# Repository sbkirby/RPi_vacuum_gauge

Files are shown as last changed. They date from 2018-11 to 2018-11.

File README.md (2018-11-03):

# Digital Vacuum Regulator with RPi
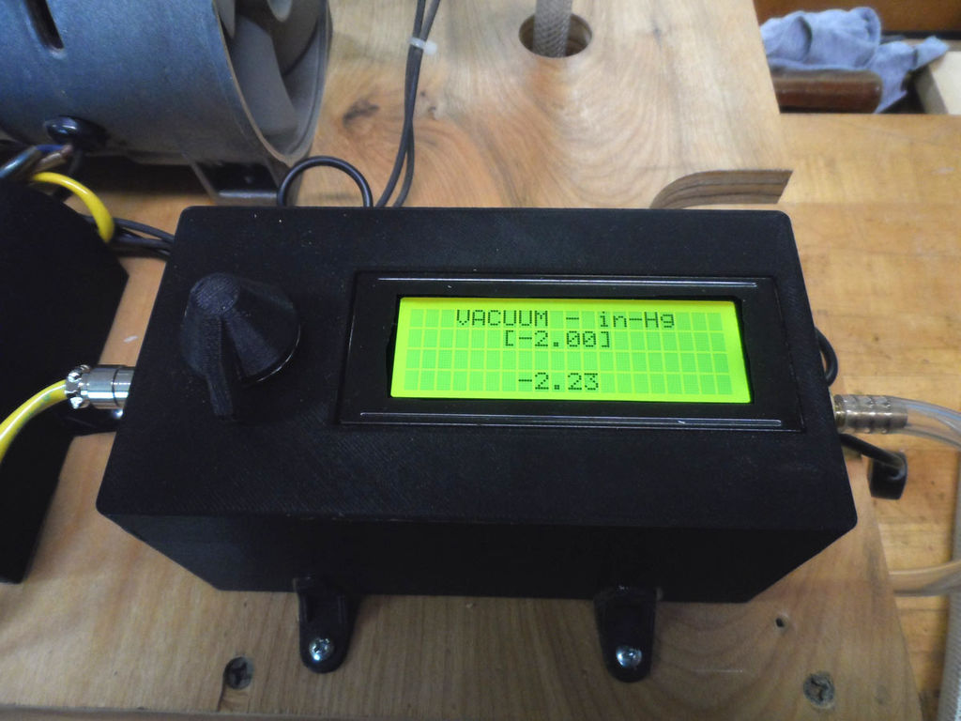
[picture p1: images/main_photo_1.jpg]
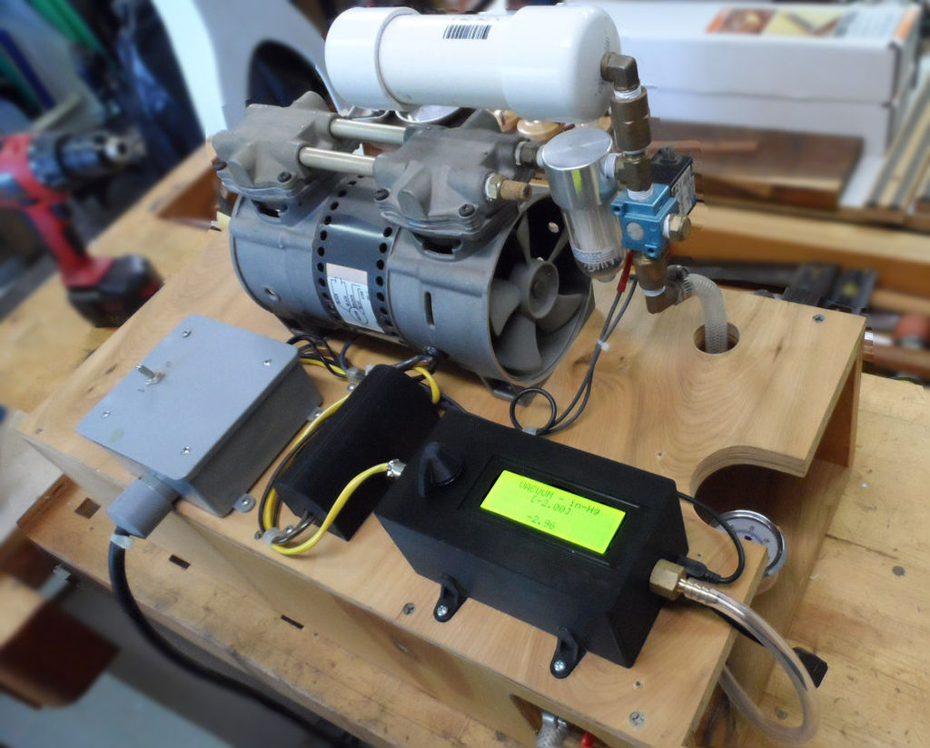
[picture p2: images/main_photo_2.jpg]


This is a Veneer Vacuum Press (Vacuum Pump) which has been modified with a Digital Vacuum Regulator to operate with a selectable vacuum pressure. This device is a replacement for the Vacuum Controller in my DIY Veneer Vacuum Press built with plans from [VeneerSupplies.com](https://www.veneersupplies.com/) or [JoeWoodworking.com](http://www.joewoodworker.com/). These are great plans and the pumps operate very satisfactorily as designed. However, I'm a tinkerer, and I wanted to enhance my pump with the ability to easily and readily control the pressure settings (without a screw driver) over a wider range of pressures with a digitally controlled regulator.

Recently, a need arose which was beyond the lower limits of my Vacuum Controller (Type 1). This project required a Type 2-Vacuum Controller for pressures in the range of 2 to 10 in-Hg. Replacing my Type 1-Vacuum Controller with a Type 2 model was an option, however, this seemed impractical since it would require an additional cost and modifications to switch between the two vacuum ranges. The ideal solution is a single controller with a wider range of pressures (2 to 28 in-Hg).

**Vacuum Controller:** A vacuum controlled micro-switch used to activate a vacuum pump or relay at a selected pressure. The vacuum controller has an adjustment screw that allows you to dial in your desired level of vacuum. The contacts are rated at 10 amps at 120v AC.

### Types of Vacuum Controller
* Type 1 = adjustable for 10.5" to 28" of Hg (Differential 2 to 5" of Hg)
* Type 2 = adjustable for 2" to 10" of Hg (Differential 2 to 4" of Hg)

## Design Considerations
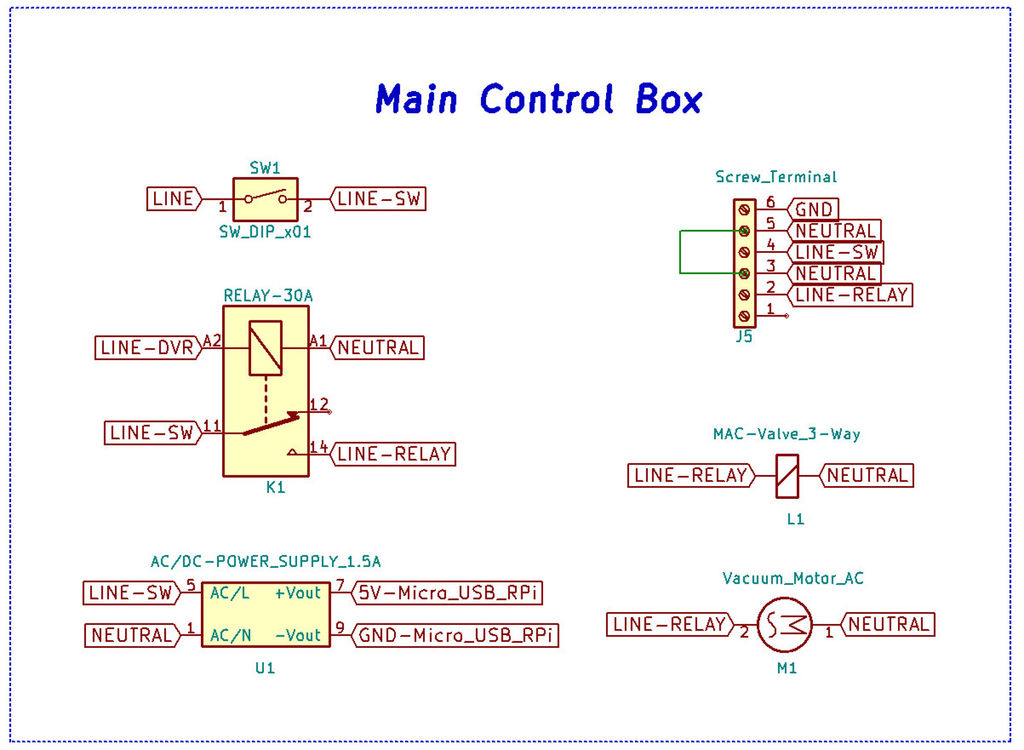
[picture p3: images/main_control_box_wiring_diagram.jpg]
Main Control Box Wiring Diagram


My design replaces the Vacuum Controller with a Digital Vacuum Regulator (DVR). The DVR will be used to control the LINE-DVR line of the RELAY-30A as seen in the Main Control Box schematic. This design requires the addition of a AC/DC 5-VDC Power Supply to Main Control Box for powering the DVR.

This design is capable of maintaining a wide range of vacuum pressures, but the performance is entirely dependent upon the capability of the pump. At the lower pressure range a large CFM pump will maintain these pressures, but result in larger differential pressure swings as a result of the displacement of the pump. This is the case for my 3 CFM pump. It is capable of maintaining 3 in-Hg, but the differential pressure swing is ±1 in-Hg, and the ON cycles of the pump, although infrequent, last approximately one or two seconds. A differential pressure swing of ±1 in-Hg will result with pressures between 141 lbs/ft² to 283 lbs/ft². I have no experience vacuum pressing at these low pressures, therefore I am not sure of the significance of this differential pressure swing. In my opinion, a smaller CFM vacuum pump would probably be more appropriate to maintain these lower vacuum pressures and reduce the differential pressure swings.

The construction of this regulator includes a Raspberry Pi Zero, MD-PS002 Pressure Sensor, HX711 Wheatstone Bridge Amplifier Module, LCD Display, 5V Power Supply, Rotary Encoder and a Relay Module. All of these parts are available from your favorite internet electronics parts suppliers.

I choose a Raspberry Pi (RPi) because python is my preferred programming language, and the support for RPi's is readily available. I am confident this application could be ported to an ESP8266 or other controllers capable of running python. The one disadvantage of the RPi is a Shutdown is highly recommended before powering it down to prevent corruption of the SD Card.

## Parts List

This device is constructed with off the shelf parts including a Raspberry Pi, Pressure Sensor, HX711 Bridge Amplifier, LCD and other parts costing approximately $25.

**PARTS:** 
* 1ea Raspberry Pi Zero - Version 1.3 $5 
* 1ea MD-PS002 Vacuum Sensor Absolute Pressure Sensor $1.75 
* 1ea HX711 Load Cell and Pressure sensor 24 bit AD module $0.75 
* 1ea KY-040 Rotary Encoder Module $1 
* 1ea 5V 1.5A 7.5W Switch Power Module 220V AC-DC Step Down Module $2.56 
* 1ea 2004 20x4 Character LCD Display Module $4.02 
* 1ea 5V 1-Channel Optocoupler Relay Module $0.99 
* 1ea Adafruit Perma-Proto Half-sized Breadboard PCB $4.50 
* 1ea 2N2222A NPN Transistor $0.09 
* 2ea 10K Resistors 
* 1ea Hose Barb Adapter 1/4" ID x 1/4" FIP $3.11 
* 1ea Brass Pipe Square Head Plug 1/4" MIP $2.96 
* 1ea GX12-2 2 Pin Diameter 12mm Male & Female Wire 
* Panel Connector Circular Screw Type Electrical Connector Socket Plug $0.67 
* 1ea Proto Box (or 3D Printed)

## Vacuum Sensor Assembly
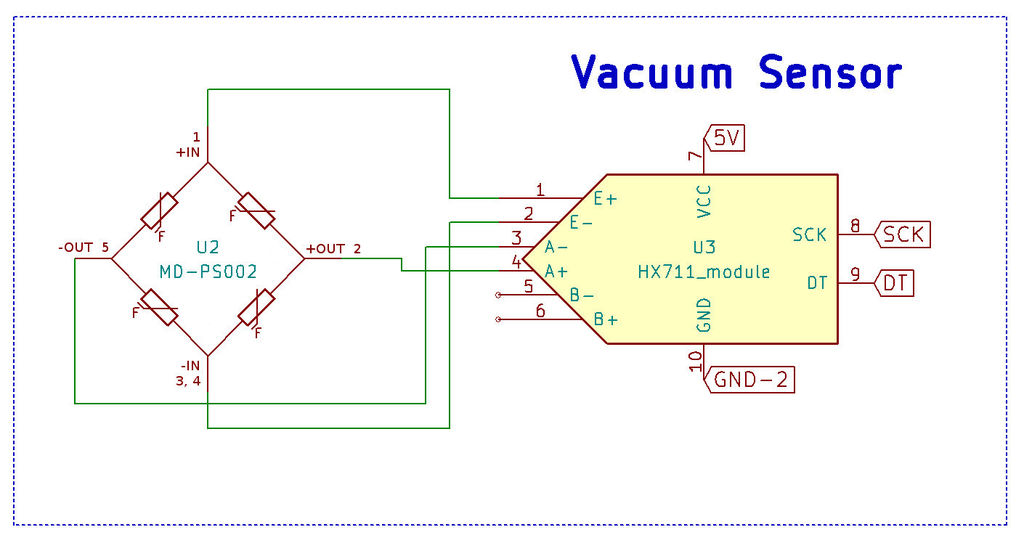
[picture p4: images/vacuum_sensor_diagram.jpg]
Vacuum Sensor Diagram


The MD-PS002 pressure sensor manufactured by Mingdong Technology (Shanghai) Co., Ltd. (MIND) has a range of 150 KPa (absolute pressure). The gauge pressure range (at sea level) for this sensor would be 49 to -101 KPa or 14.5 to -29.6 in-Hg. These sensors are readily available on eBay, banggood, aliexpress and other online sites. However, the specifications listed by a few of these suppliers are conflicting, therefore, I've included a translated "Technical Parameters" sheet from a Mingdong Technology.

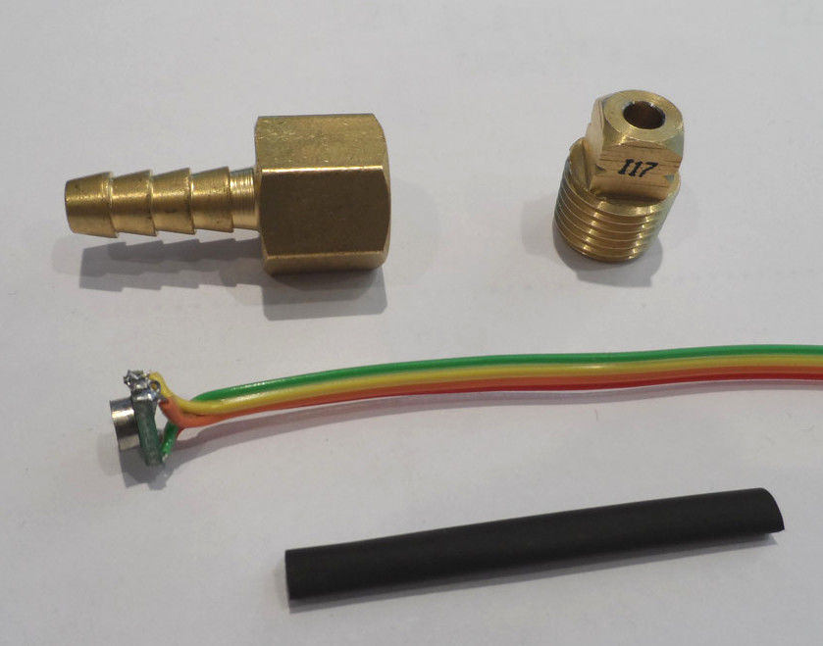
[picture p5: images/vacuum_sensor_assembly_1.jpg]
Vacuum Sensor Assembly


Connecting the sensor to a HX711 Load Cell and Pressure sensor 24 bit AD module requires the following: connect Pins 3 & 4 together; Pin 1 (+IN) to E+; Pin 3 & 4 (-IN) to E-; Pin 2 (+OUT) to A+ and Pin 5 (-OUT) to A- of the HX711 module. Prior to packaging the wired sensor in a brass adapter, cover the leads and the exposed edges of the sensor with heat shrink tubing or electrical tape. Insert and center the sensor over the barbed nipple opening, and then use clear silicone caulking to seal the sensor inside the adapter while taking care to keep the caulking away from the sensor face. A Brass Pipe Square Head Plug which has been drilled with a hole large enough to accommodate the sensor wire is threaded over the wire, filled with silicone caulking and screwed onto the barbed adapter. Wipe excess caulking from the assembly, and wait 24 hours for the caulking to dry before testing.

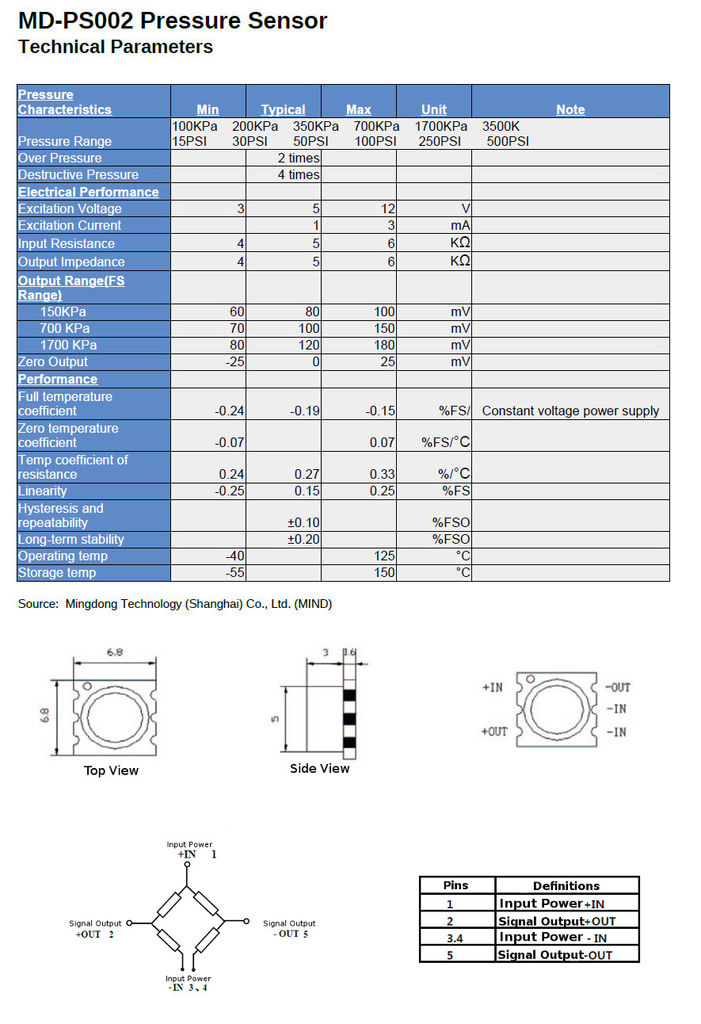
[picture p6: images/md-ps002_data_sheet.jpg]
MD-PS002 Data Sheet


## Electronics Assembly
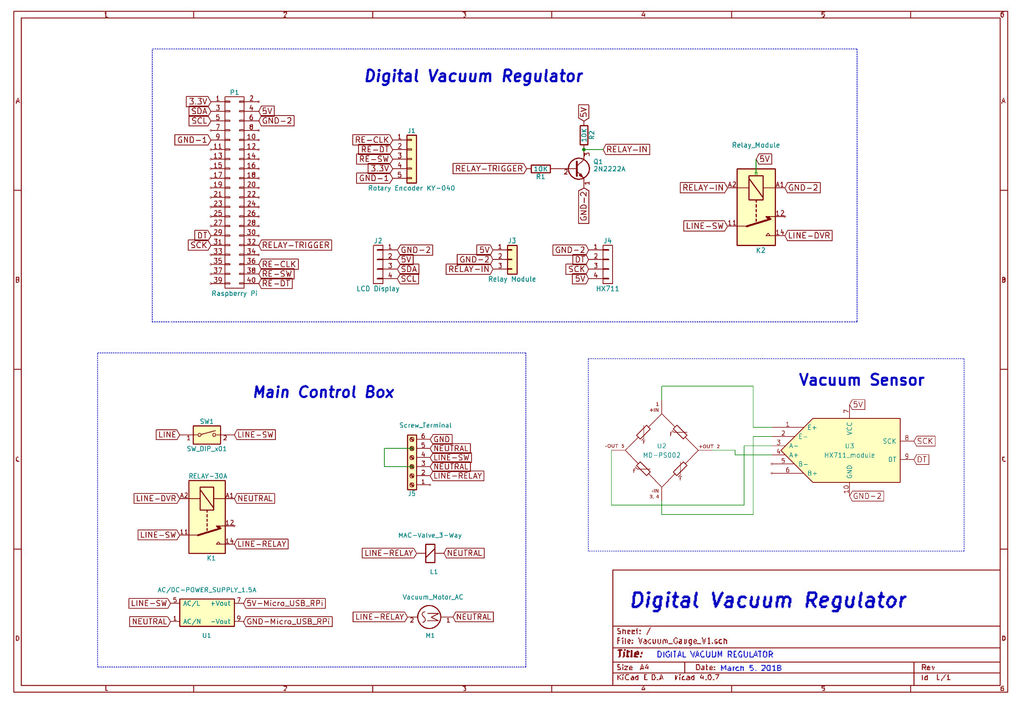
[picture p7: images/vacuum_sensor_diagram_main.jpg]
Main Wiring Diagram


The electronics consist of a Raspberry Pi Zero (RPi) connected to an HX711 module with a MD-PS002 pressure sensor, KY-040 Rotary Encoder, Relay Module and a LCD display. The Rotary Encoder is interfaced to the RPi via Pin 21 to the DT of the encoder, Pin 16 to the CLK and Pin 20 to the SW or switch of the encoder. The pressure sensor is connected to the HX711 module, and the DT and SCK pins of this module are connected directly to Pin 5 and 6 of the RPi. The Relay Module is triggered by a 2N2222A transistor circuit which is connected to RPi Pin 32 for a trigger source. The Normally Open contacts of the Relay Module are connected to LINE-SW and one side of the coil of the 30A RELAY. Power and Ground for the Digital Vacuum Regulator are supplied by Pins 1, 4, 6 and 9 of the RPi. Pin 4 is the 5v power pin, which is connected directly to the RPi's power input. Details of the connections can be seen in the Digital Vacuum Regulator schematic.

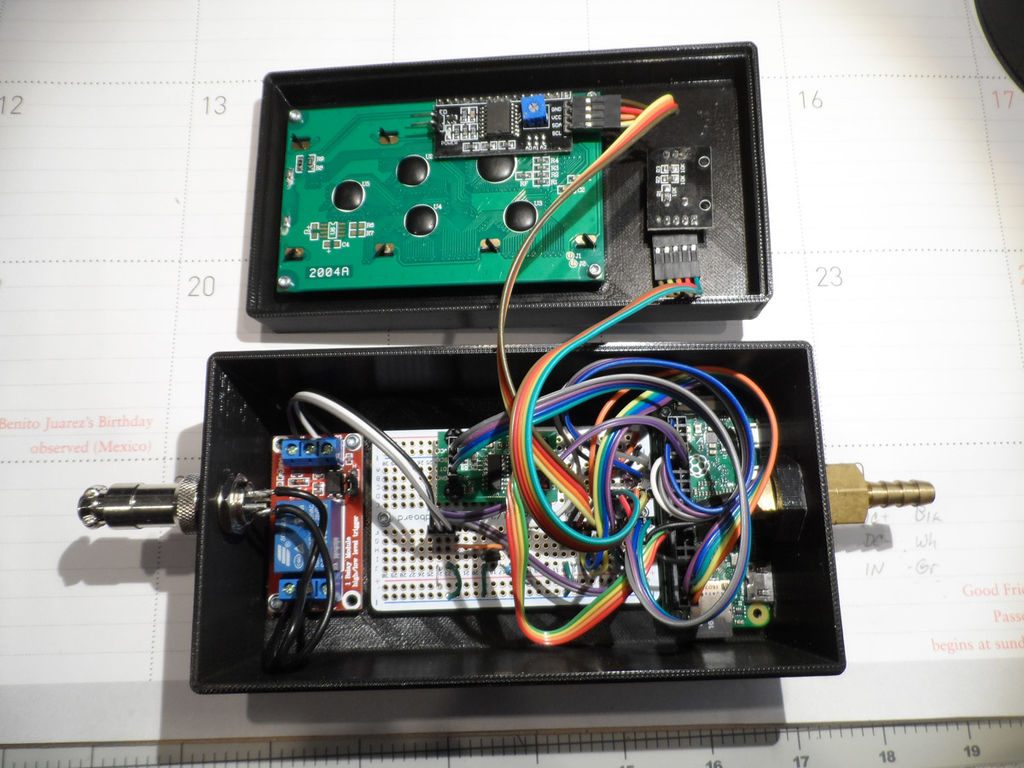
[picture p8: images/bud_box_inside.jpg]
Bud Box Inside


## Update and Configure the Raspberry Pi
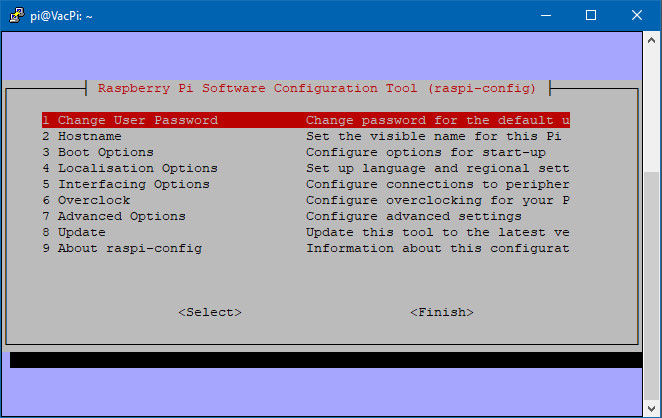
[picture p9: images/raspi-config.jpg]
raspi-config


Update the existing software on your Raspberry Pi (RPi) with the following command lines instructions
```
sudo apt-get update
sudo apt-get upgrade
```
Depending on how out-of-date your RPi is at the time will determine the amount of time needed to complete these commands.
Next, the RPi needs to be configured for I2C communications via Raspi-Config.
```
sudo raspi-config
```
The screen seen above will appear. First select Advanced Options and then Expand Filesystem and select Yes. After returning to the Main Menu of Raspi-Config select Enable Boot to Desktop/Scratch and choose to Boot to Console. From the Main Menu select Advanced Options, and enable I2C and SSH from the available options. Finally, select Finish and reboot the RPi.

## Software
Log into the RPi and create the following directories. The /Vac_Sensor contains the program files and /logs will contain the crontab log files.
```
cd ~
mkdir Vac_Sensor
mkdir logs
cd Vac_Sensor
```
Copy the files above to the /Vac_Sensor folder. I use WinSCP to connect and manage the files on the RPi. Connection to the RPi maybe done via Wifi or serial connection, but SSH needs be enabled in raspi-config to allow this type of connection.

The primary program is vac_sensor.py and may be run from the command prompt. In order to test the script enter the following:
```
sudo python vac_sensor.py
```
As mentioned previously, the vac_sensor.py script is the primary file for the scale. It imports the hx711.py file to read the vacuum sensor via HX711 module. The version of hx711.py used for my project comes from [tatobari/hx711py](https://github.com/tatobari/hx711py). I found this version provided the features I wanted.

The LCD requires the RPi_I2C_driver.py by Denis Pleic and forked by Marty Tremblay, and can be found at [MartyTremblay/RPi_I2C_driver.py](https://gist.github.com/MartyTremblay/7a7fbf76c0c93734511b).

Rotary Encoder by Peter Flocker can be found at [https://github.com/petervflocke/rotaryencoder_rpi](https://github.com/petervflocke/rotaryencoder_rpi)

pimenu by Alan Aufderheide can be found at [https://github.com/skuater/pimenu](https://github.com/skuater/pimenu)

The config.json file contains the data stored by the program, and some items can be modified by menu options. This file is updated and saved at Shutdown. The "units" can be setup via the Units menu option either as in-Hg (default), mm-Hg or psi. The "vacuum_set" is the cutoff pressure, and is stored as in-Hg value, and is modified by the Cutoff Pressure menu option. A "calibration_factor" value is manually set in the config.json file, and is determined by calibrating the vacuum sensor to a vacuum gauge. The "offset" is value created by Tare, and can be set via this menu option. The "cutoff_range" is manually set in the config.json file, and is the differential pressure range of the "vacuum_set" value.

Cutoff Value = "vacuum_set" ± (("cutoff_range"/100) x "vacuum_set")

Please note your "calibration_factor" and "offset" may differ from those I have. Example config.json file:
```
{"units": 0, "vacuum_set": -15.0, "calibration_factor": 230000, "cutoff_range": 0.5, "offset": 11448294}
```

## Calibration
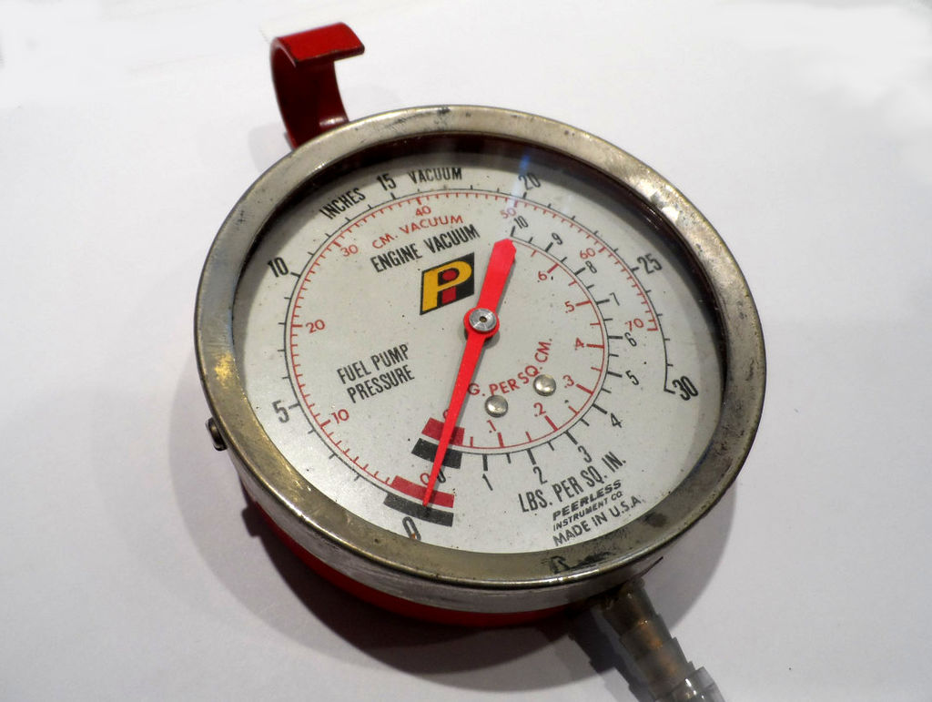
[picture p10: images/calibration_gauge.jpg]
Calibration Gauge


Calibration is much easier to do using SSH and running the following commands:
```
cd Vac_Sensor 
sudo python vac_sensor.py
```
Exiting the python script can be done via Ctrl-C, and modifications can be made to the /Vac_Sensor/config.json file.

Calibrating the vacuum sensor requires an accurate vacuum gauge, and adjusting the "calibration_factor" to match the output displayed on the LCD. First, use the Tare menu option to set and save the "offset" value with the pump at atmospheric pressure. Next, turn the pump ON with the Vacuum menu and after the pressure settles read the LCD display and compare this to vacuum gauge. Turn the pump OFF and Exit the script. Adjust the "calibration_factor" variable located in /Vac_Sensor/config.json file. Restart the script and repeat the process with exception of Tare. Make the necessary adjustments to the "calibration_factor" until the LCD display matches the gauge reading.

The "calibration_factor" and "offset" affect the display via the following calculations:

get_value = read_average - "offset"

pressure = get_value/"calibration_factor"

I used an old Peerless Engine Vacuum Gauge to calibrate the regulator instead of the vacuum gauge on my pump because it had been knocked out calibration. The Peerless gauge is 3-3/4" (9.5 cm) in diameter and much easier to read.

## Run at Startup
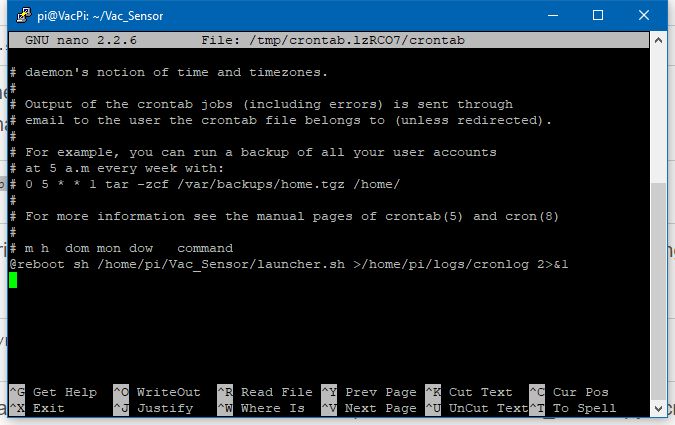
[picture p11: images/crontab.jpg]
Crontab


There's an excellent Instructable [Raspberry Pi: Launch Python script on startup](https://www.instructables.com/id/Raspberry-Pi-Launch-Python-script-on-startup/?ALLSTEPS) for running a scripts at startup.

Log into the RPi and change to the /Vac_Sensor directory.
```
cd /Vac_Sensor
nano launcher.sh
```
Include the following text in launcher.sh
```
#!/bin/sh
# launcher.sh
# navigate to home directory, then to this directory, then execute python script, then back home
cd /
cd home/pi/Vac_Sensor
sudo python vac_sensor.py
cd /
```
Exit and save the launcher.sh

We need to make the script an executable.
```
chmod 755 launcher.sh
```
Test the script.
```
sh launcher.sh
```
Next, we need to edit crontab (the linux task manager) to launch the script at startup. Note: we have already created the /logs directory previously.
```
sudo crontab -e
```
This will bring the crontab window as seen above. Navigate to the end of the file and enter the following line.
```
@reboot sh /home/pi/Vac_Sensor/launcher.sh >/home/pi/logs/cronlog 2>&1
```
Exit and save the file, and reboot the RPi. The script should start the vac_sensor.py script after the RPi reboots. The status of the script can be checked in the log files located in the /logs folder.

## Operational Instructions

For Operational Instructions visit [Digital Vacuum Regulator](https://www.instructables.com/id/Digital-Vacuum-Regulator/) on Instructables.

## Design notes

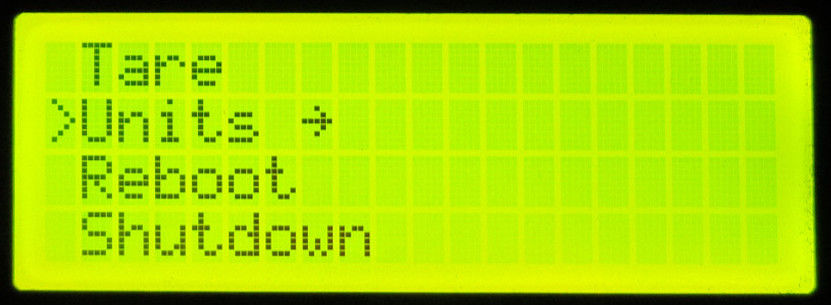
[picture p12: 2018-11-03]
images/menu_units.jpg

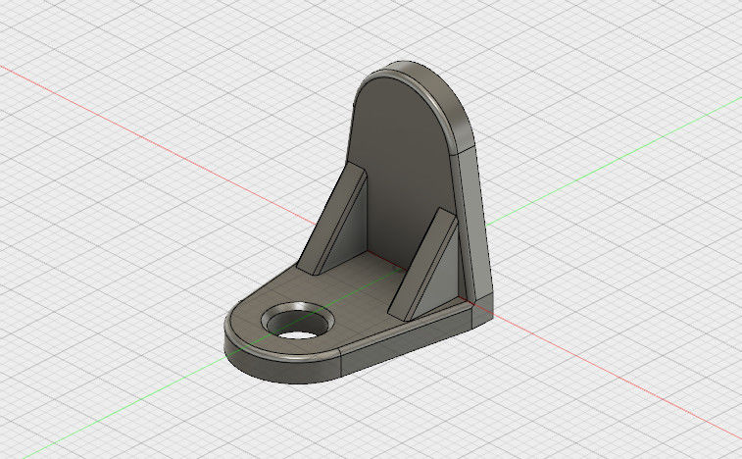
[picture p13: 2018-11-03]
images/model_of_tab.jpg

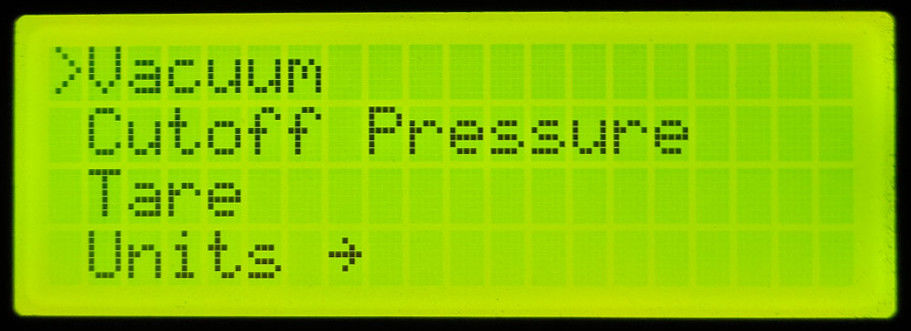
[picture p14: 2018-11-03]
images/main_menu.jpg

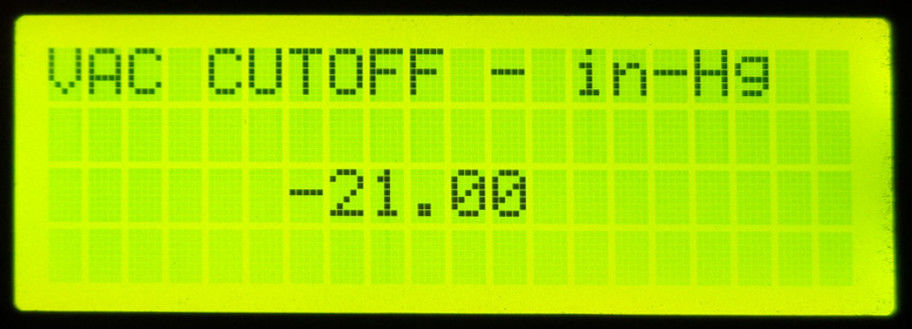
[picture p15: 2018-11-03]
images/cutoff_pressure.jpg

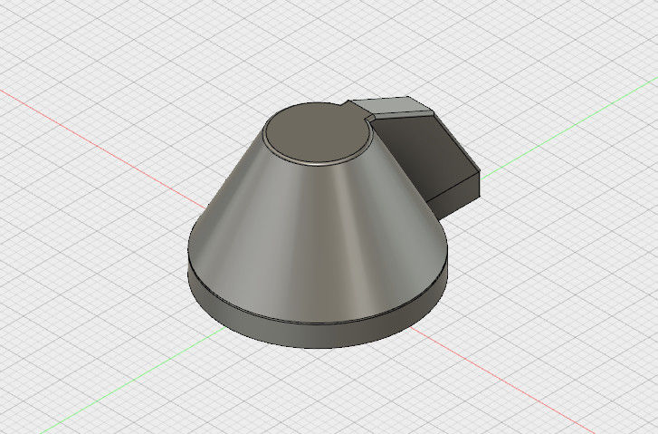
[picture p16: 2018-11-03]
images/model_of_knob.jpg

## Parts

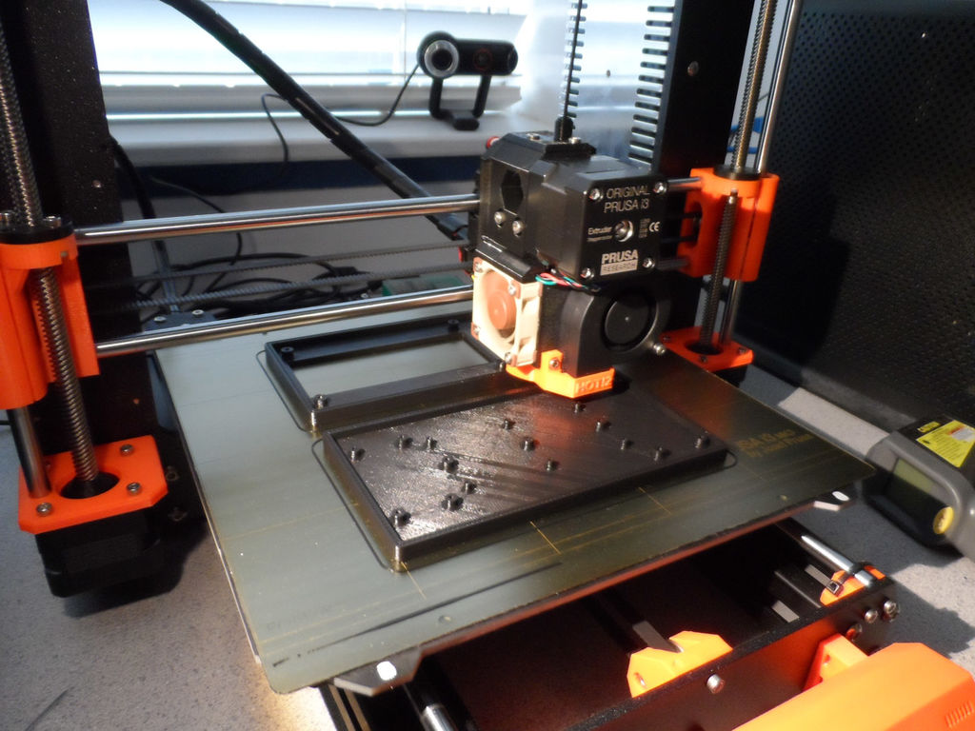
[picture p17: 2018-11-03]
images/3d_printing_parts.jpg

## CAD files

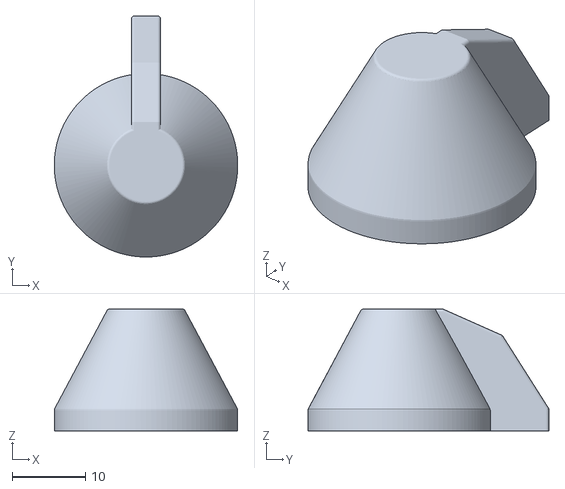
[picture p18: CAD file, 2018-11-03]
stl/Knob_for_KY-040_Rotary_Encoder.stl
25.0 x 32.8 x 16.6

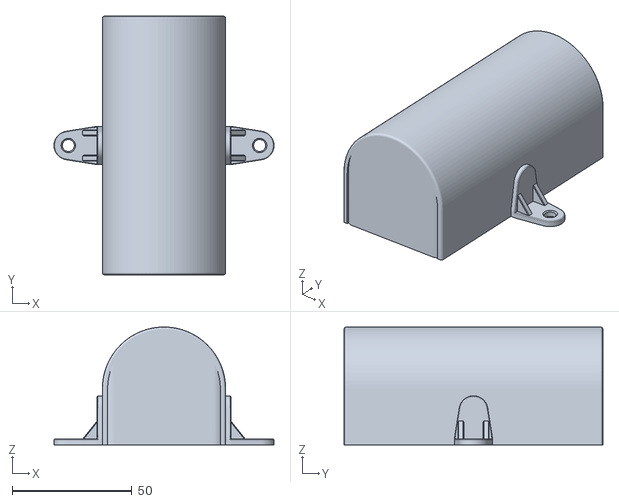
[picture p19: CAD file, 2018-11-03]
stl/Capacitor_Cover.stl
91.8 x 108.0 x 49.2

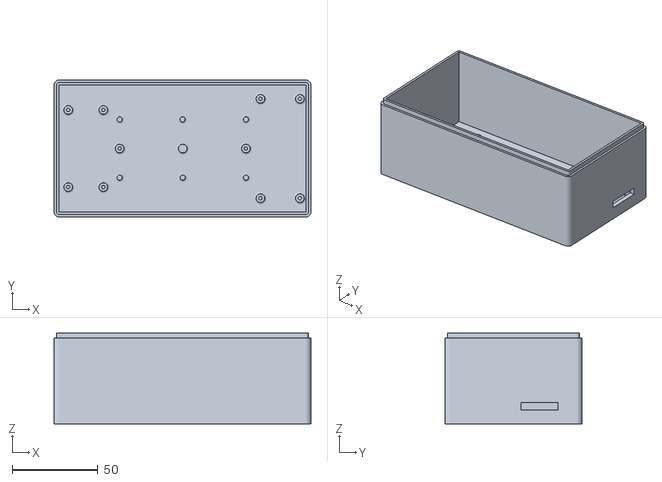
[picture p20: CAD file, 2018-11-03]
stl/Base.stl
150.0 x 80.0 x 53.0

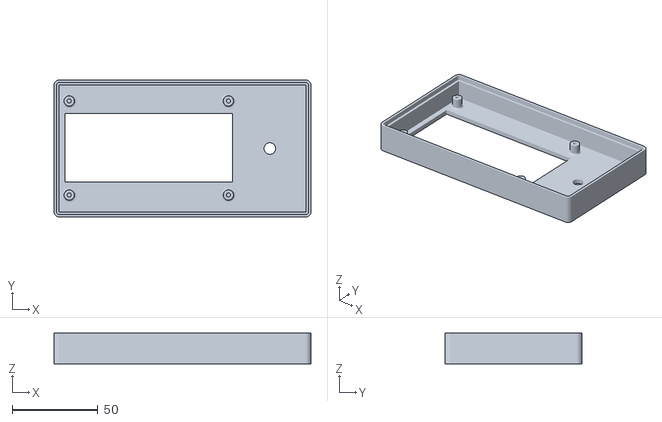
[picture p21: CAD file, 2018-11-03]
stl/Top.stl
150.0 x 80.0 x 18.0

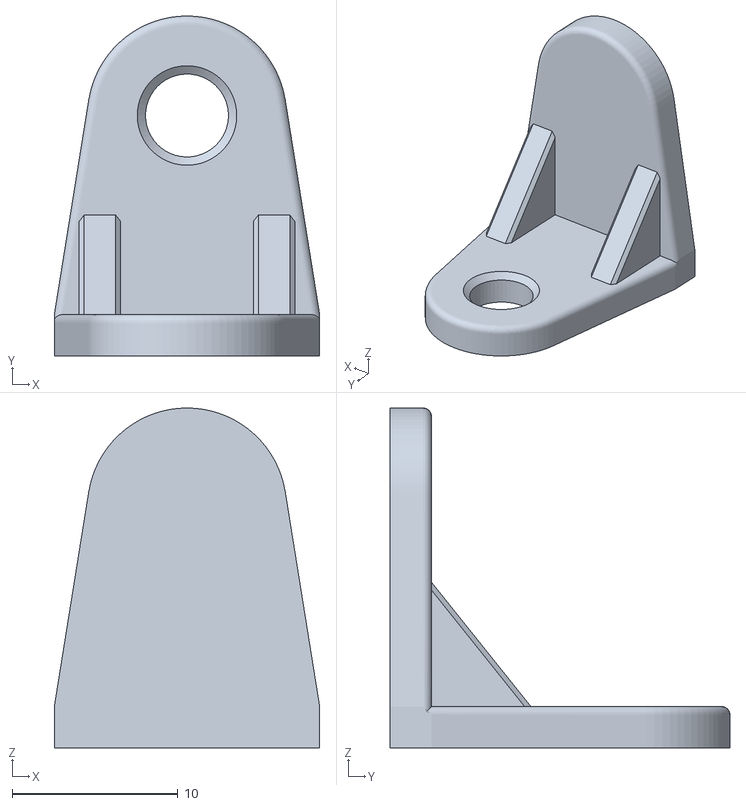
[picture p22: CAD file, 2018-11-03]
stl/Screw_Bracket.stl
16.0 x 20.5 x 20.5

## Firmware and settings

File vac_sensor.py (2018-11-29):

#!/usr/bin/python
#
# Originally lcdmenu.py created by Alan Aufderheide, February 2013
# Modified by Stephen Kirby, November 2017
#
# This provides a menu driven application using the Adafruit_CharLCDPlate
# driver

import commands
import os
from string import split
from time import sleep, strftime, localtime
from datetime import datetime, timedelta
from xml.dom.minidom import *

import smbus

import json
import sys
from Queue import Queue
import RotaryEncoder
import RPi_I2C_driver
from hx711 import HX711
import RPi.GPIO as GPIO

# Load configuration from config JSON file.
with open('config.json', 'r') as infile:
    config = json.load(infile)

menu_file = 'vac_menu.xml' # Menu Tree

# Rotary Encoder wiring
A_PIN  = 21 # A pin on rotary encoder or DT on KY040
B_PIN  = 16 # B pin on rotary encoder or CLK on KY040
SW_PIN = 20 # press pin on rotary or SW on KY040

# Init Queue and Encoder
RotQueue = Queue()                                                              # define global queue for events
encoder = RotaryEncoder.RotaryEncoderWorker(A_PIN, B_PIN, SW_PIN, RotQueue)     # create a new rotary switch

# set DEBUG=1 for print debug statements
DEBUG = 0
DISPLAY_ROWS = 4
DISPLAY_COLS = 20

# set to 0 if you want the LCD to stay on, 1 to turn off and on auto
AUTO_OFF_LCD = 0

# Menu Folders to display Selected items
menu_select = ["units"]

# init LCD
lcd = RPi_I2C_driver.lcd()
lcd.lcd_clear()
lcd.backlight(1) # turn ON LED

# HX711(dout, sck) - initialize Wheatstone Bridge amplifier
hx = HX711(5, 6)  # DOUT = GPIO.IN, SCK = GPIO.OUT
# The value on the Gauge = value / self.REFERENCE_UNIT
hx.set_reference_unit(config['calibration_factor'])
# Reset and set offset for the HX711 amplifier board
hx.reset()
hx.set_offset(config['offset']) # set offset for MD-PS002 Pressure Sensor
hx.tare(5) # with no Vacuum on Sensor

# Init GPIO output port for Relay control
GPIO.setmode(GPIO.BCM)
GPIO.setup(12, GPIO.OUT)
GPIO.output(12, False) # Turn OFF Relay

# save data to config.json data file
def save_data():
    with open('config.json', 'w') as outfile:
        json.dump(config, outfile)

# save the data, cleanup GPIO and exit
def clean_and_exit(doExit):
    save_data() # save data file
    lcd.lcd_clear() # clear LCD
    sleep(0.1)
    lcd.backlight(0) # turn OFF LED
    sleep(0.1)
    GPIO.cleanup() # cleanup GPIO
    if doExit:
        sys.exit() #exit python to system

def DoShutdown():
    lcd.lcd_clear()
    lcd.message("Shutting Down!")
    sleep(3)
    clean_and_exit(False)
    commands.getoutput("sudo shutdown -h now")

def DoReboot():
    lcd.lcd_clear()
    lcd.message("I'm Rebooting!")
    sleep(3)
    clean_and_exit(False)
    commands.getoutput("sudo reboot")

# Go BACK in the Menu
def DoBack():
    lcd.lcd_clear()
    display.update('l')
    #display.update('s')
    display.display()
    sleep(0.05)

# Calculate Cutoff range
def SetCutoffRange(state):
    # Range of Vacuum Pump activation
    cutoff_range = config['cutoff_range'] / 100
    if state == 'ON':
        return (-cutoff_range * config["vacuum_set"]) + config["vacuum_set"]
    if state == 'OFF':
        return (cutoff_range * config["vacuum_set"]) + config["vacuum_set"]

# Fetch Units String
def GetUnit():
    if config['units'] == 0: # in-Hg    DEFAULT
        unit = 'in-Hg'
    elif config['units'] == 1: # mm-Hg
        unit = 'mm-Hg'
    elif config['units'] == 2: # psi
        unit = 'psi'
    return unit

# Convert from in-Hg to other units
def ConvertVac(vac):
    if config['units'] == 0: # in-Hg    DEFAULT
        vac *= 1.0
    elif config['units'] == 1: # mm-Hg
        vac *= 25.3285
    elif config['units'] == 2: # psi
        vac *= 0.48977
    return vac

# Select Units
def SetinHg(): #DEFAULT
    config['units'] = 0
    display.display()

def SetmmHg():
    config['units'] = 1
    display.display()

def Setpsi():
    config['units'] = 2
    display.display()

# Display Vacuum and Cutoff on LCD Display
def DoDisplay():
    lcd.lcd_clear()
    unit = GetUnit()
    VacSet = ConvertVac(config['vacuum_set'])
    VacSetOFF = ConvertVac(SetCutoffRange('OFF'))
    VacSetON = ConvertVac(SetCutoffRange('ON'))
    GPIO.output(12, False) # Turn OFF Relay
    if DEBUG:
        print('OFF: {0:.2f}'.format(VacSetOFF) + ' ' + unit)
        print('ON: {0:.2f}'.format(VacSetON) + ' ' + unit)

    while True:
        # Read Vacuum Sensor
        val = VacVal = ConvertVac(hx.get_weight(1))
        if DEBUG:
            print('{0:.2f}'.format(VacVal) + ' ' + unit)
        # Monitor Vacuum Cutoff Value
        if VacVal <= VacSetOFF:
            GPIO.output(12, False) # Turn OFF Relay
            #sleep(0.05)
        elif VacVal > VacSetON:
            GPIO.output(12, True) # Turn ON Relay
            #sleep(0.05)
        # Display Results
        lcd.home()
        lcd.message('   VACUUM - ' + unit + '\n      [{0:.2f}]'.format(VacSet) + '\n\n')
        lcd.message('       {0:.2f}'.format(val))
        # Reset Wheatstone Bridge
        hx.power_down()
        hx.power_up()
        # Read RotaryEncoder
        if not(RotQueue.empty()):
            m = RotQueue.get_nowait()
            if (m == RotaryEncoder.EventDown): #SELECT
                GPIO.output(12, False) # Turn OFF Relay on Exit
                RotQueue.task_done()
                DoBack()
                return
            RotQueue.task_done()

# Display and set Cutoff Vacuum
def SetCutoff():
    lcd.lcd_clear()
    unit = GetUnit()
    while True:
        # Prints the weight. Comment if you're debbuging the MSB and LSB issue.
        val = ConvertVac(config["vacuum_set"]) # Stored in in-Hg reguardless of units selected
        if DEBUG:
            print('{0:.2f}'.format(val) + ' ' + unit)
        lcd.home()
        lcd.message('VAC CUTOFF - ' + unit + '\n\n')
        lcd.message('      {0:.2f}'.format(val))
        # Read RotaryEncoder
        if not(RotQueue.empty()):
            m = RotQueue.get_nowait()
            if (m == RotaryEncoder.EventDown): #SELECT - Exit
                RotQueue.task_done()
                DoBack()
                return
            if (m == RotaryEncoder.EventLeft): #LEFT - Subtract
                config["vacuum_set"] -= 0.25
            if (m == RotaryEncoder.EventRight): #RIGHT - Add
                config["vacuum_set"] += 0.25
            RotQueue.task_done()

# Tare Vacuum Sensor
def DoTare():
    lcd.lcd_clear()
    lcd.message('\n Tare Vac Sensor\n')
    hx.reset()
    hx.set_offset(config['offset']) # set offset for MD-PS002 Pressure Sensor
    hx.tare(5) # with no Vacuum on Sensor
    config['offset'] = hx.OFFSET # read and store the OFFSET
    save_data() # save the new OFFSET to config.json data file
    sleep(3)

def ShowIPAddress():
    if DEBUG:
        print('in ShowIPAddress')
    lcd.lcd_clear()
    lcd.message(commands.getoutput("/sbin/ifconfig").split("\n")[1].split()[1][5:])
    while True:
        if not(RotQueue.empty()):
            m = RotQueue.get_nowait()
            if (m == RotaryEncoder.EventDown): #SELECT
                DoBack()
                return
            RotQueue.task_done()

# Classes Used in Menus
class CommandToRun:
    def __init__(self, myName, theCommand):
        self.text = myName
        self.commandToRun = theCommand
    def Run(self):
        self.clist = split(commands.getoutput(self.commandToRun), '\n')
        if len(self.clist) > 0:
            lcd.lcd_clear()
            lcd.message(self.clist[0])
            lcd.crlf()
            for i in range(1, len(self.clist)):
                while not(RotQueue.empty()):
                    m=RotQueue.get_nowait()
                    if m == RotaryEncoder.EventLeft: #DOWN
                        break
                    RotQueue.task_done()
                    #sleep(0.25)
                lcd.lcd_clear()
                lcd.message(self.clist[i-1]+'\n'+self.clist[i])
                lcd.crlf()
                sleep(0.5)
        while not(RotQueue.empty()):
            m=RotQueue.get_nowait()
            if m == RotaryEncoder.EventRight:  #UP
                break
            RotQueue.task_done()

class Widget:
    def __init__(self, myName, myFunction):
        self.text = myName
        self.function = myFunction

class Folder:
    def __init__(self, myName, myParent):
        self.text = myName
        self.items = []
        self.parent = myParent

# Process menu items based on type
def ProcessNode(currentNode, currentItem):
    children = currentNode.childNodes

    for child in children:
        if isinstance(child, xml.dom.minidom.Element):
            if child.tagName == 'folder':
                thisFolder = Folder(child.getAttribute('text'), currentItem)
                currentItem.items.append(thisFolder)
                ProcessNode(child, thisFolder)
            elif child.tagName == 'widget':
                thisWidget = Widget(child.getAttribute('text'), child.getAttribute('function'))
                currentItem.items.append(thisWidget)
            elif child.tagName == 'run':
                thisCommand = CommandToRun(child.getAttribute('text'), child.firstChild.data)
                currentItem.items.append(thisCommand)

class Display:
    def __init__(self, folder):
        self.curFolder = folder
        self.curTopItem = 0
        self.curSelectedItem = 0
    def display(self):
        isSelected = match_selected = ''
        # Check for Bottom of items list
        if self.curTopItem > len(self.curFolder.items) - DISPLAY_ROWS:
            self.curTopItem = len(self.curFolder.items) - DISPLAY_ROWS
        # Check for Top of items list
        if self.curTopItem < 0:
            self.curTopItem = 0
        if DEBUG:
            print('------------------')
        if self.curFolder.text[0:self.curFolder.text.find(' ')].lower() in menu_select:
            isSpace = self.curFolder.text.find(' ')
            if isSpace < 0:
                isSpace = self.curFolder.text.len()
            isSelected = self.curFolder.text[0:isSpace].lower()
        str = ''
        for row in range(self.curTopItem, self.curTopItem + DISPLAY_ROWS):
            if isSelected != '':
                if isSelected == 'units':
                    match_selected = GetUnit()
            if row > self.curTopItem:
                str += '\n'
            if row < len(self.curFolder.items):
                # Is row the current selected line
                if row == self.curSelectedItem:
                    # Current line with cursor
                    cmd = '>' + self.curFolder.items[row].text
                    if self.curFolder.items[row].text.lower() == match_selected.lower():
                        cmd += '*'
                    if len(cmd) < DISPLAY_COLS:
                        # Add spaces to END of line
                        for row in range(len(cmd), DISPLAY_COLS):
                            cmd += ' '
                    if DEBUG:
                        print('|'+cmd+'|')
                    str += cmd
                # If NOT currently selected line
                else:
                    # Lines without cursor - Add space for NO cursor
                    cmd = ' '+self.curFolder.items[row].text
                    if self.curFolder.items[row].text.lower() == match_selected.lower():
                        cmd += '*'
                    if len(cmd) < DISPLAY_COLS:
                        # Add spaces to END of line
                        for row in range(len(cmd), DISPLAY_COLS):
                            cmd += ' '
                    if DEBUG:
                        print('|'+cmd+'|')
                    str += cmd
        if DEBUG:
            print('------------------')
        lcd.lcd_clear()
        lcd.home()
        lcd.message(str)

    # Orignal update() designed for LCD with 4 Buttons (Left, Right, Up, Down)
    # This function has been utilized as follows:
    # UP = Clockwise knob turn
    # DOWN = Counter clockwise knob turn
    # SELECT = Press knob DOWN
    def update(self, command):
        global currentLcd
        global lcdstart
        #lcd.backlight(currentLcd)
        lcdstart = datetime.now()
        if DEBUG:
            print('do',command)
        if command == 'u':
            self.up()
        elif command == 'd':
            self.down()
        elif command == 'r':
            self.right()
        elif command == 'l':
            self.left()
        elif command == 's':
            self.select()

    def up(self):
        if self.curSelectedItem == 0:
            return
        elif self.curSelectedItem > self.curTopItem:
            self.curSelectedItem -= 1
        else:
            self.curTopItem -= 1
            self.curSelectedItem -= 1

    def down(self):
        if self.curSelectedItem+1 == len(self.curFolder.items):
            return
        elif self.curSelectedItem < self.curTopItem+DISPLAY_ROWS-1:
            self.curSelectedItem += 1
        else:
            self.curTopItem += 1
            self.curSelectedItem += 1

    def left(self):
        if isinstance(self.curFolder.parent, Folder):
            # find the current in the parent
            itemno = 0
            index = 0
            for item in self.curFolder.parent.items:
                if self.curFolder == item:
                    if DEBUG:
                        print('foundit')
                    index = itemno
                else:
                    itemno += 1
            if index < len(self.curFolder.parent.items):
                self.curFolder = self.curFolder.parent
                self.curTopItem = index
                self.curSelectedItem = index
            else:
                self.curFolder = self.curFolder.parent
                self.curTopItem = 0
                self.curSelectedItem = 0

    def right(self):
        if isinstance(self.curFolder.items[self.curSelectedItem], Folder):
            self.curFolder = self.curFolder.items[self.curSelectedItem]
            self.curTopItem = 0
            self.curSelectedItem = 0
        elif isinstance(self.curFolder.items[self.curSelectedItem], Widget):
            if DEBUG:
                print('eval', self.curFolder.items[self.curSelectedItem].function)
            eval(self.curFolder.items[self.curSelectedItem].function+'()')
        elif isinstance(self.curFolder.items[self.curSelectedItem], CommandToRun):
            self.curFolder.items[self.curSelectedItem].Run()

    def select(self):
        if DEBUG:
            print('check widget')
        if isinstance(self.curFolder.items[self.curSelectedItem], Widget):
            if DEBUG:
                print('eval', self.curFolder.items[self.curSelectedItem].function)
            eval(self.curFolder.items[self.curSelectedItem].function+'()')

# Process Rotary Encoder Actions with a Queue
def process():
    # this function can be called in order to decide what is happening with the switch
    while True:
        if not(RotQueue.empty()):
            m=RotQueue.get_nowait()
            # DOWN = Counter clockwise knob turn
            if m == RotaryEncoder.EventLeft: #DOWN
                display.update('d') #DOWN
                display.display()
                sleep(0.1)
            # SELECT = Press knob DOWN
            if m == RotaryEncoder.EventDown: #SELECT
                display.update('r') #RIGHT
                #display.update('s') #SELECT
                display.display()
                sleep(0.1)
            # UP = Clockwise knob turn
            if m == RotaryEncoder.EventRight: #UP
                display.update('u') #UP
                display.display()
                sleep(0.1)

            if AUTO_OFF_LCD:
                lcdtmp = lcdstart + timedelta(seconds=5)
                if (datetime.now() > lcdtmp):
                    #lcd.backlight(lcd.OFF)
                    #sleep(0.1)
                    pass
            RotQueue.task_done()

# now start things up
uiItems = Folder('root','')

dom = parse(menu_file) # parse an XML file by name

top = dom.documentElement

currentLcd = False
#lcd.backlight(lcd.OFF)
ProcessNode(top, uiItems)

display = Display(uiItems)
display.display()

if DEBUG:
    print('start while')

lcdstart = datetime.now()

if __name__ == "__main__":
    try:
        while True:
            if DEBUG:
                print('__main__')
            #sleep (0.01)  # here you can process on RPI whatever you want and operate the rotary knob it won't be missed
            process()  # and check what has happened with rotary
    except KeyboardInterrupt:
        print('broken by keyboard')
        clean_and_exit(True)

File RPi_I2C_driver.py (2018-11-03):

# -*- coding: utf-8 -*-
"""
Compiled, mashed and generally mutilated 2014-2015 by Denis Pleic
Made available under GNU GENERAL PUBLIC LICENSE

# Modified Python I2C library for Raspberry Pi
# as found on http://www.recantha.co.uk/blog/?p=4849
# Joined existing 'i2c_lib.py' and 'lcddriver.py' into a single library
# added bits and pieces from various sources
# By DenisFromHR (Denis Pleic)
# 2015-02-10, ver 0.1

A large amount of the code was included from Adafruit_CharLCDPlate

"""
#
#
import smbus
from time import *

class i2c_device:
   def __init__(self, addr, port=1):
      self.addr = addr
      self.bus = smbus.SMBus(port)

# Write a single command
   def write_cmd(self, cmd):
      self.bus.write_byte(self.addr, cmd)
      sleep(0.0001)

# Write a command and argument
   def write_cmd_arg(self, cmd, data):
      self.bus.write_byte_data(self.addr, cmd, data)
      sleep(0.0001)

# Write a block of data
   def write_block_data(self, cmd, data):
      self.bus.write_block_data(self.addr, cmd, data)
      sleep(0.0001)

# Read a single byte
   def read(self):
      return self.bus.read_byte(self.addr)

# Read
   def read_data(self, cmd):
      return self.bus.read_byte_data(self.addr, cmd)

# Read a block of data
   def read_block_data(self, cmd):
      return self.bus.read_block_data(self.addr, cmd)



class lcd:
    # LCD Address
    ADDRESS = 0x27

    # commands
    LCD_CLEARDISPLAY = 0x01
    LCD_RETURNHOME = 0x02
    LCD_ENTRYMODESET = 0x04
    LCD_DISPLAYCONTROL = 0x08
    LCD_CURSORSHIFT = 0x10
    LCD_FUNCTIONSET = 0x20
    LCD_SETCGRAMADDR = 0x40
    LCD_SETDDRAMADDR = 0x80

    # flags for display entry mode
    LCD_ENTRYRIGHT = 0x00
    LCD_ENTRYLEFT = 0x02
    LCD_ENTRYSHIFTINCREMENT = 0x01
    LCD_ENTRYSHIFTDECREMENT = 0x00

    # flags for display on/off control
    LCD_DISPLAYON = 0x04
    LCD_DISPLAYOFF = 0x00
    LCD_CURSORON = 0x02
    LCD_CURSOROFF = 0x00
    LCD_BLINKON = 0x01
    LCD_BLINKOFF = 0x00

    # flags for display/cursor shift
    LCD_DISPLAYMOVE = 0x08
    LCD_CURSORMOVE = 0x00
    LCD_MOVERIGHT = 0x04
    LCD_MOVELEFT = 0x00

    # flags for function set
    LCD_8BITMODE = 0x10
    LCD_4BITMODE = 0x00
    LCD_2LINE = 0x08
    LCD_1LINE = 0x00
    LCD_5x10DOTS = 0x04
    LCD_5x8DOTS = 0x00

    # flags for backlight control
    LCD_BACKLIGHT = 0x08
    LCD_NOBACKLIGHT = 0x00

    # Offset for up to 4 rows.
    LCD_ROW_OFFSETS         = (0x00, 0x40, 0x14, 0x54)

    # Line addresses for up to 4 line displays.  Maps line number to DDRAM address for line.
    LINE_ADDRESSES = { 1: 0xC0, 2: 0x94, 3: 0xD4 }

    # Truncation constants for message function truncate parameter.
    NO_TRUNCATE       = 0
    TRUNCATE          = 1
    TRUNCATE_ELLIPSIS = 2

    En = 0b00000100 # Enable bit
    Rw = 0b00000010 # Read/Write bit
    Rs = 0b00000001 # Register select bit

    #initializes objects and lcd
    def __init__(self):
        self.lcd_device = i2c_device(self.ADDRESS)

        # Initialize display control, function, and mode registers.
        self.displaycontrol = self.LCD_DISPLAYON | self.LCD_CURSOROFF | self.LCD_BLINKOFF
        self.displayfunction = self.LCD_4BITMODE | self.LCD_1LINE | self.LCD_2LINE | self.LCD_5x8DOTS
        self.displaymode = self.LCD_ENTRYLEFT | self.LCD_ENTRYSHIFTDECREMENT

        self.lcd_write(0x03)
        self.lcd_write(0x03)
        self.lcd_write(0x03)
        self.lcd_write(0x02)

        # Write registers.
        self.lcd_write(self.LCD_DISPLAYCONTROL | self.displaycontrol)
        self.lcd_write(self.LCD_FUNCTIONSET | self.displayfunction)
        self.lcd_write(self.LCD_ENTRYMODESET | self.displaymode)  # set the entry mode

        sleep(0.2)

    # clocks EN to latch command
    def lcd_strobe(self, data):
        self.lcd_device.write_cmd(data | self.En | self.LCD_BACKLIGHT)
        sleep(.0005)
        self.lcd_device.write_cmd(((data & ~self.En) | self.LCD_BACKLIGHT))
        sleep(.0001)

    def lcd_write_four_bits(self, data):
        self.lcd_device.write_cmd(data | self.LCD_BACKLIGHT)
        self.lcd_strobe(data)

    # write a command to lcd
    def lcd_write(self, cmd, mode=0):
        self.lcd_write_four_bits(mode | (cmd & 0xF0))
        self.lcd_write_four_bits(mode | ((cmd << 4) & 0xF0))

    # write a character to lcd (or character rom) 0x09: backlight | RS=DR<
    # works!
    def lcd_write_char(self, charvalue, mode=1):
        self.lcd_write_four_bits(mode | (charvalue & 0xF0))
        self.lcd_write_four_bits(mode | ((charvalue << 4) & 0xF0))

    # put string function
    def lcd_display_string(self, string, line):
        if line == 1:
            self.lcd_write(0x80)
        if line == 2:
            self.lcd_write(0xC0)
        if line == 3:
            self.lcd_write(0x94)
        if line == 4:
            self.lcd_write(0xD4)

        for char in string:
            self.lcd_write(ord(char), self.Rs)

    # clear lcd and set to home
    def lcd_clear(self):
        self.lcd_write(self.LCD_CLEARDISPLAY)
        self.lcd_write(self.LCD_RETURNHOME)

    # define backlight on/off (lcd.backlight(1); off= lcd.backlight(0)
    def backlight(self, state): # for state, 1 = on, 0 = off
        if state == 1:
            self.lcd_device.write_cmd(self.LCD_BACKLIGHT)
        elif state == 0:
            self.lcd_device.write_cmd(self.LCD_NOBACKLIGHT)

    # add custom characters (0 - 7)
    def lcd_load_custom_chars(self, fontdata):
        self.lcd_write(0x40);
        for char in fontdata:
            for line in char:
                self.lcd_write_char(line)

    # define precise positioning (addition from the forum)
    def lcd_display_string_pos(self, string, line, pos):
        if line == 1:
            pos_new = pos
        elif line == 2:
            pos_new = 0x40 + pos
        elif line == 3:
            pos_new = 0x14 + pos
        elif line == 4:
            pos_new = 0x54 + pos

        self.lcd_write(0x80 + pos_new)

        for char in string:
            self.lcd_write(ord(char), self.Rs)
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

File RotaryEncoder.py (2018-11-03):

import RPi.GPIO as GPIO
import math
import threading
from Queue import Queue

EventLeft  = 'L'
EventRight = 'R'
EventUp    = 'U'
EventDown  = 'D'


class RotaryEncoderWorker(object):

    def __init__(self, a_pin, b_pin, s_pin, Q):

        self.gpio = GPIO
        self.gpio.setwarnings(False)
        self.queue = Q

        self.a_pin = a_pin
        self.b_pin = b_pin
        self.s_pin = s_pin

        self.gpio.setmode(GPIO.BCM)
        #Rotary
        self.gpio.setup(self.a_pin, self.gpio.IN, pull_up_down=self.gpio.PUD_UP)
        self.gpio.setup(self.b_pin, self.gpio.IN, pull_up_down=self.gpio.PUD_UP)

        self.gpio.add_event_detect(self.a_pin, GPIO.BOTH, callback=self.RotaryCall)
        self.gpio.add_event_detect(self.b_pin, GPIO.BOTH, callback=self.RotaryCall)

        #Switch
        self.gpio.setup(self.s_pin, self.gpio.IN, pull_up_down=self.gpio.PUD_UP)
        self.gpio.add_event_detect(self.s_pin, GPIO.BOTH, callback=self.SwitchCall, bouncetime=50) # depending on hardware the debouncing can be done by software or hardware here we used software version 

        self.SWPrev = 1

        self.last_delta = 0
        self.r_seq = 0

        # steps_per_cycle and remainder are only used in get_cycles which
        # returns a coarse-granularity step count.  By default
        # steps_per_cycle is 4 as there are 4 steps per
        # detent on my encoder, and get_cycles() will return -1 or 1
        # for each full detent step.
        self.steps_per_cycle = 4
        self.remainder = 0
        self.cycles = 0

        #self.lock = threading.Lock()
        self.delta = 0

    def SwitchCall(self, channel):
        state = self.gpio.input(self.s_pin)
        if state == 0:
            if self.SWPrev == 1:
                #print ("Switch Down")
                self.SWPrev = 0
                self.queue.put(EventDown)
            else: #still pressed
                pass
        else: # state = 1
            if self.SWPrev == 0:
                #print ("Switch Up")
                self.SWPrev = 1
                self.queue.put(EventUp)
            else: #still pressed
                pass

    # Inspired by http://guy.carpenter.id.au/gaugette/blog/2013/01/14/rotary-encoder-library-for-the-raspberry-pi/
    # Returns the quadrature encoder state converted into
    # a numerical sequence 0,1,2,3,0,1,2,3...
    #
    # Turning the encoder clockwise generates these
    # values for switches B and A:
    #  B A
    #  0 0
    #  0 1
    #  1 1
    #  1 0
    # We convert these to an ordinal sequence number by returning
    #   seq = (A ^ B) | B << 2

    def RotaryCall(self, channel):
        delta = 0
        a_state = self.gpio.input(self.a_pin)
        b_state = self.gpio.input(self.b_pin)
        r_seq = (a_state ^ b_state) | b_state << 1
        if r_seq != self.r_seq:
            delta = (r_seq - self.r_seq) % 4
            if delta==3:
                delta = -1
            elif delta==2:
                delta = int(math.copysign(delta, self.last_delta))  # same direction as previous, 2 steps
            self.last_delta = delta
            self.r_seq = r_seq
        self.delta += delta
        self.remainder += delta #self.get_delta()
        self.cycles = self.remainder // self.steps_per_cycle
        self.remainder %= self.steps_per_cycle # remainder always remains positive
        # Check rotary status
        if self.cycles == 1:
            self.queue.put(EventLeft)
            self.delta = 0
        elif self.cycles == -1:
            self.queue.put(EventRight)
            self.delta = 0
        else:
            pass

    # it does not work as expected fix me
    def __del__(self):
        self.gpio.cleanup()
        
    #workaround to close gpio in a proper way, function shall be called at exit 
    def Exit(self):
        self.gpio.cleanup()
        
        

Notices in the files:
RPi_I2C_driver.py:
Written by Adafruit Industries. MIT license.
